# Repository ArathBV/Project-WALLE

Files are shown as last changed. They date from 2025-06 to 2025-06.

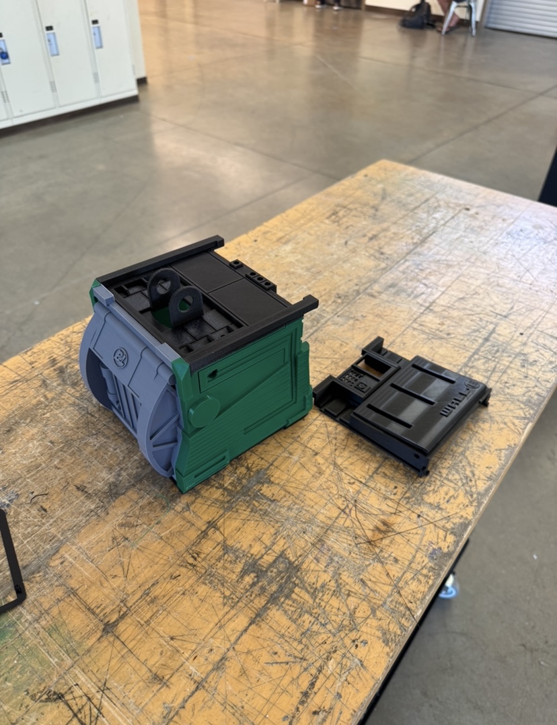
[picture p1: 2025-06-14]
docs/firstPrint.PNG

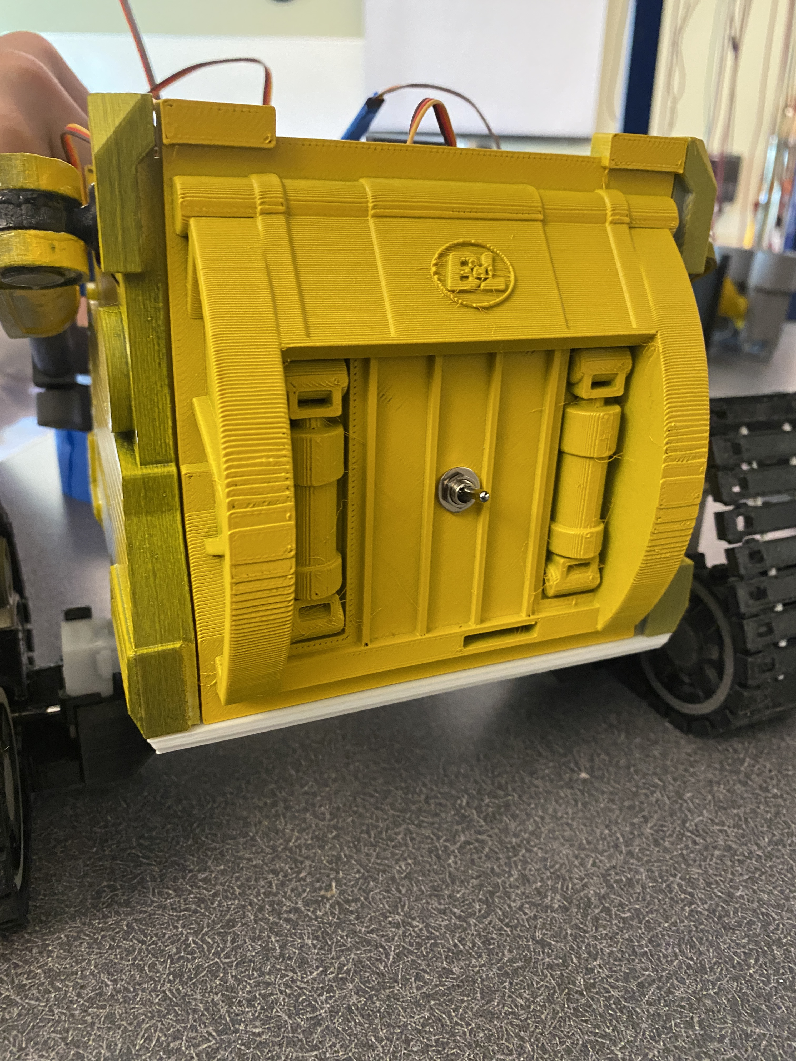
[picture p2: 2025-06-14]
docs/images/WALLE_ESTOP.JPG

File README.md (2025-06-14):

# Project-WALLE
## Authors: Arath Villanueva, Devon Bolt
### Repository Overview
- This repository contains a folder of Doxygen items, WALL-E source code found in Codes, and Hardware Design aspects both mechanical and electrical in the Hardware folder.
### Project Website and Documentation
Project in depth details and website https://arathbv.github.io/Project-WALLE/index.html

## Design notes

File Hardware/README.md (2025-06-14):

# WALL-E Hardware Files
- This folder contains the Mechanical design files and the PCB design files. 
- The Mechanical desing components were changed based on the electronic and peripherals that were used for this WALL-E project.
- The WALL-E PCB Folder contains the WALL-E motheboard that was created for this project
- All original and remaining WALL-E CAD and step files can be found at https://wired.chillibasket.com/3d-printed-wall-e/

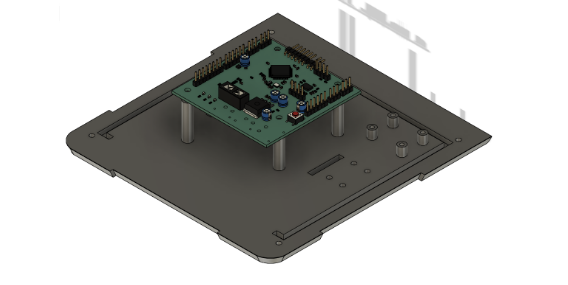
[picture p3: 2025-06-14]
docs/BottomPanelCAD.png

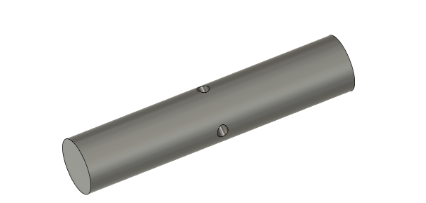
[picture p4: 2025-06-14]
docs/HandAxleCAD.png

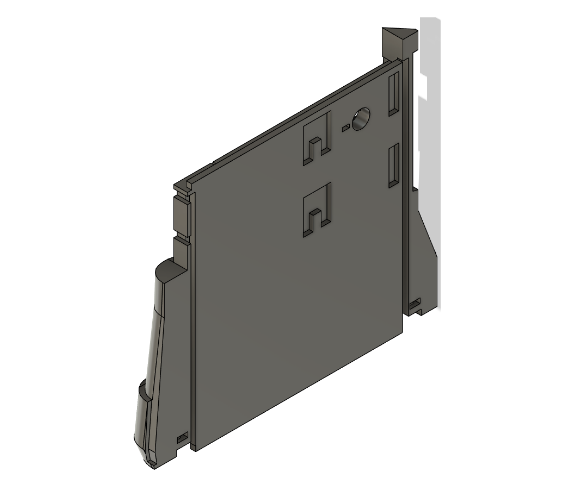
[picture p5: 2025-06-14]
docs/RightBodyPanelCAD.png

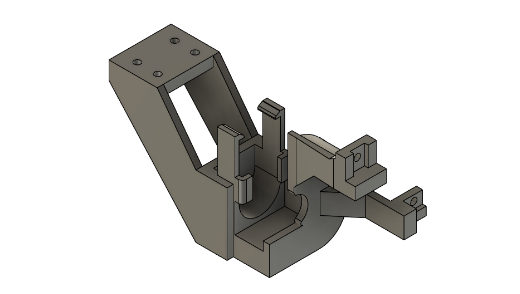
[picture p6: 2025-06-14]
docs/MotorMountCAD.png

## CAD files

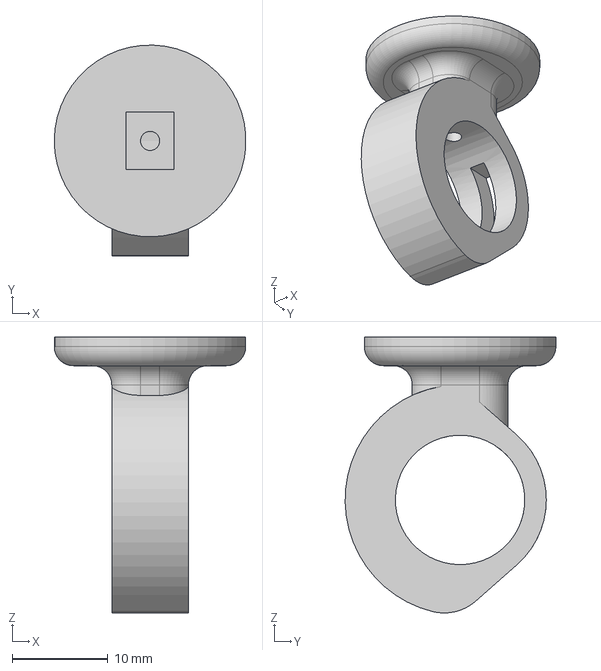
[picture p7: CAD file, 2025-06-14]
Hardware/Mechanical Design Modified Files/Arm Files/arm-hinge-outer-x2 v3.step
20.0 x 22.0 x 28.8 mm

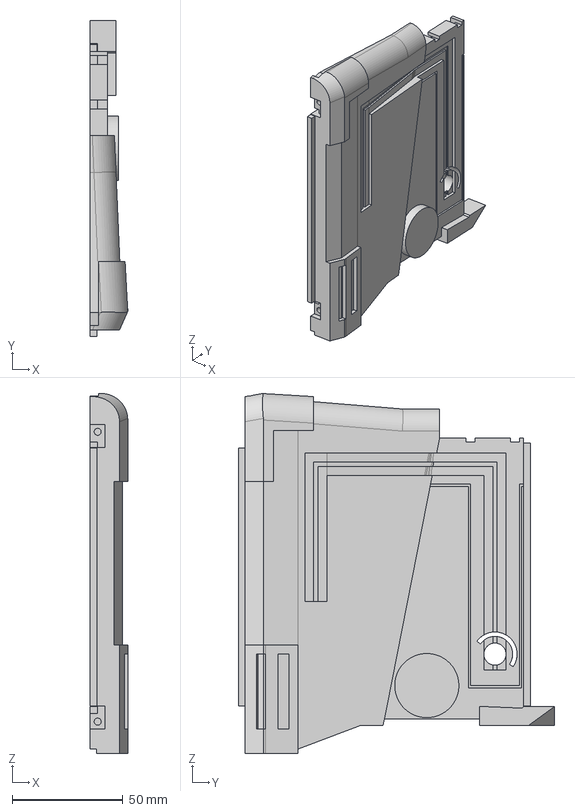
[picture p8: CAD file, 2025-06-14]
Hardware/Mechanical Design Modified Files/Body Files/body-left v4.step
17.0 x 143.0 x 162.7 mm

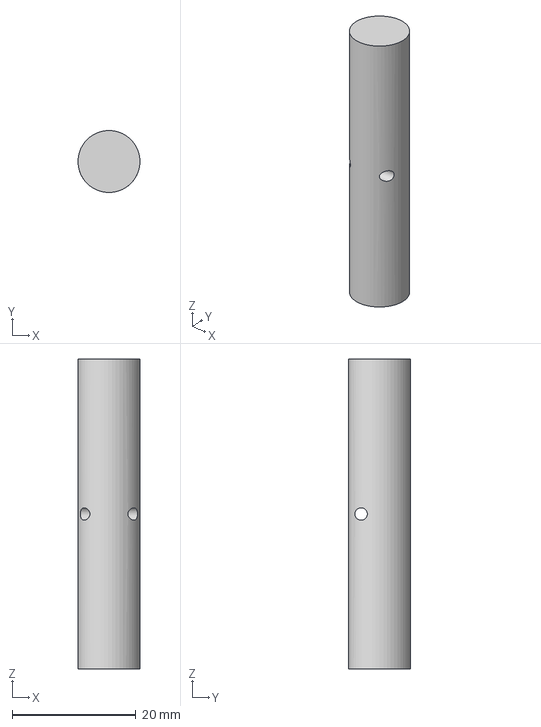
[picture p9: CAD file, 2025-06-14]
Hardware/Mechanical Design Modified Files/Hand Files/hand-axel-x2 v2.step
9.99 x 10.00 x 50.0 mm

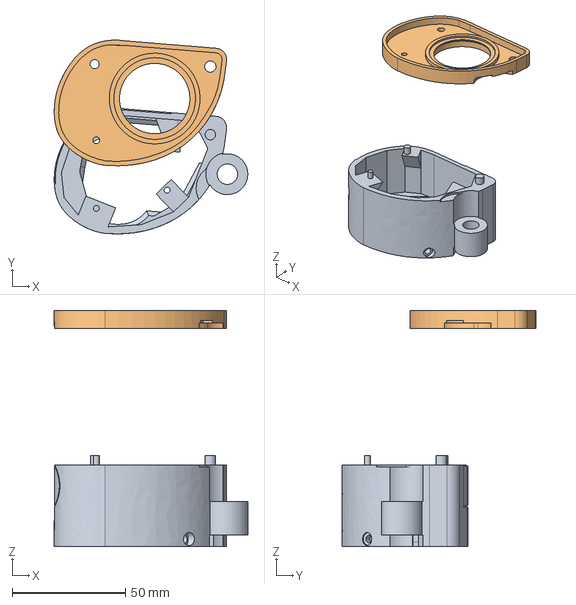
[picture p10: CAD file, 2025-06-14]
Hardware/Mechanical Design Modified Files/Head Files/eye-front-right v11.step
85.3 x 85.4 x 104.0 mm

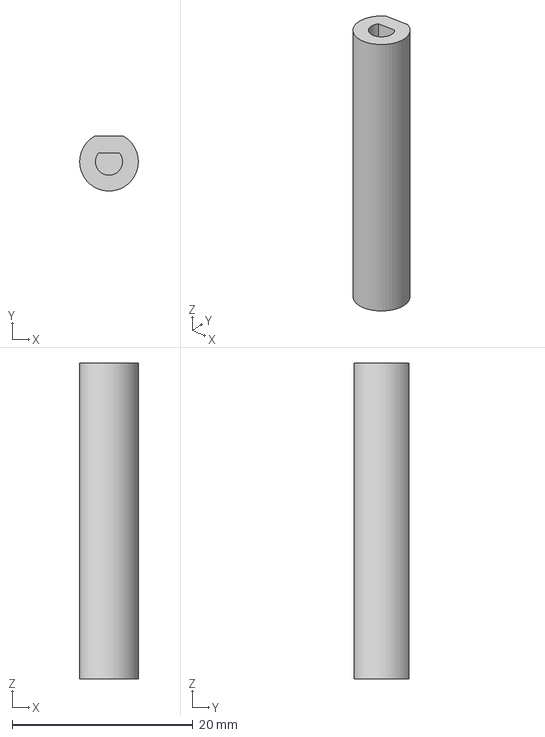
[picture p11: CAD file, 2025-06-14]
Hardware/Mechanical Design Modified Files/Wheel Files/wheel-bracket-outer-left v10.step
6.50 x 6.09 x 35.0 mm

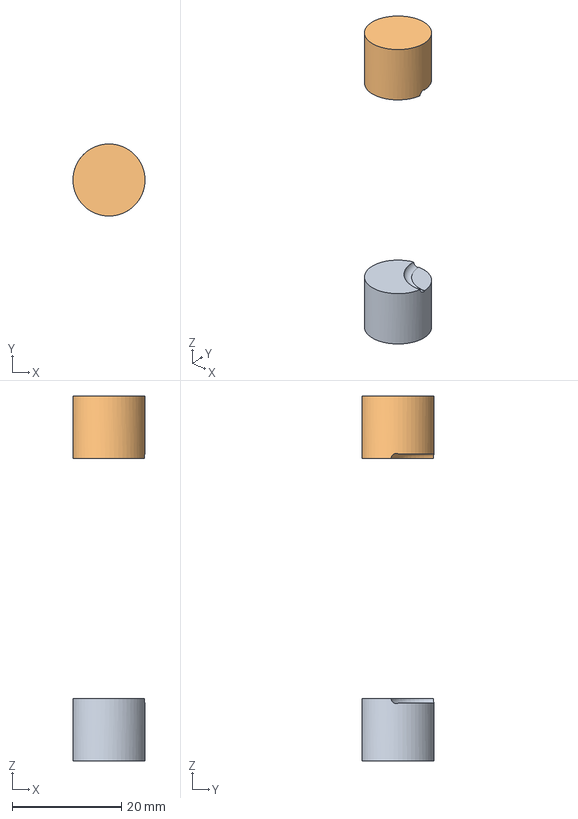
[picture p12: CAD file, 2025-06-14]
Hardware/Mechanical Design Modified Files/Arm Files/arm-hinge-axel-x2 v3.step
13.2 x 13.2 x 66.8 mm

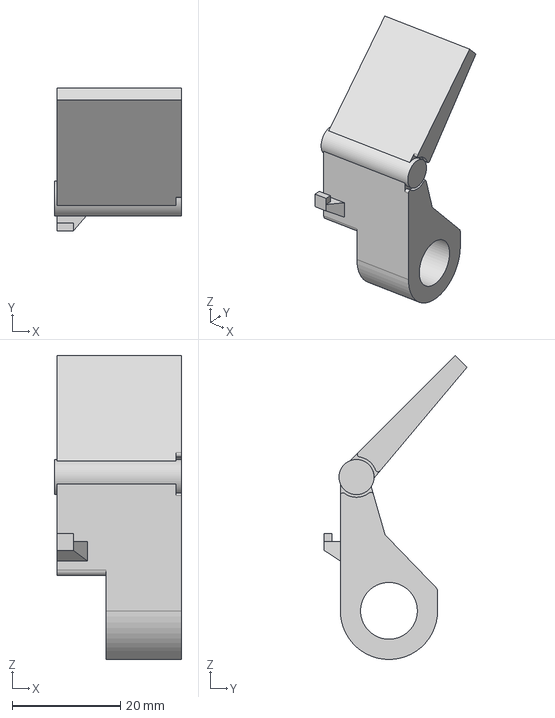
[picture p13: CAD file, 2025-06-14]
Hardware/Mechanical Design Modified Files/Hand Files/hand-finger-left-x2 v2.step
23.5 x 26.4 x 56.2 mm

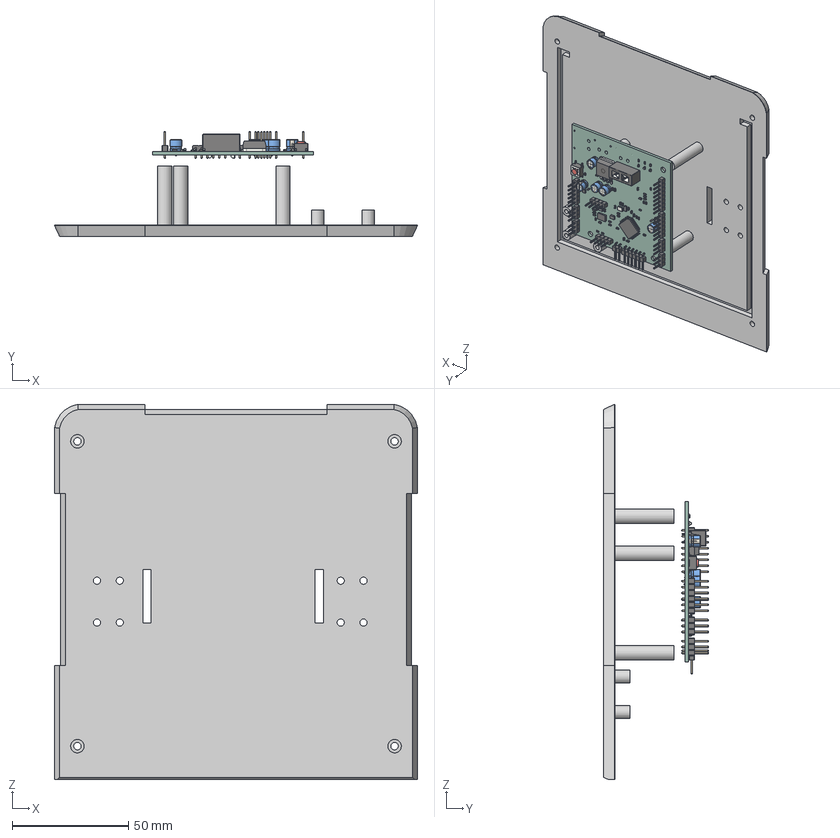
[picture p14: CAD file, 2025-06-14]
Hardware/Mechanical Design Modified Files/Body Files/body-bottom v12.step
156.0 x 45.2 x 161.3 mm
LQFP_64_10x10mm_P05mm
C_0603_1608Metric_23 x 23
R_0603_1608Metric_21 x 21
CP_Radial_D50mm_P200mm x 5
PinHeader_1x06_P254mm_Horizontal
PinHeader_1x02_P254mm_Horizontal
Crystal_SMD_3215-2Pin_3.2x1.5mm_2 x 2
LED_0603_1608Metric_3 x 3
PinHeader_1x04_P254mm_Vertical x 2
PinHeader_1x03_P254mm_Vertical x 4
WSON_8_1EP_2x2mm_P05mm_EP09x16mm x 2
LGA_28_52x38mm_P05mm
A_Keystone_3568
PinHeader_1x06_P254mm_Vertical x 2
PinHeader_1x08_P254mm_Vertical
SW_SPST_PTS645_1
L_1008_2520Metric_1
CQ assembly
Crystal_SMD_3225-4Pin_3.2x2.5mm_1
Wall_E_motherboard_PCB

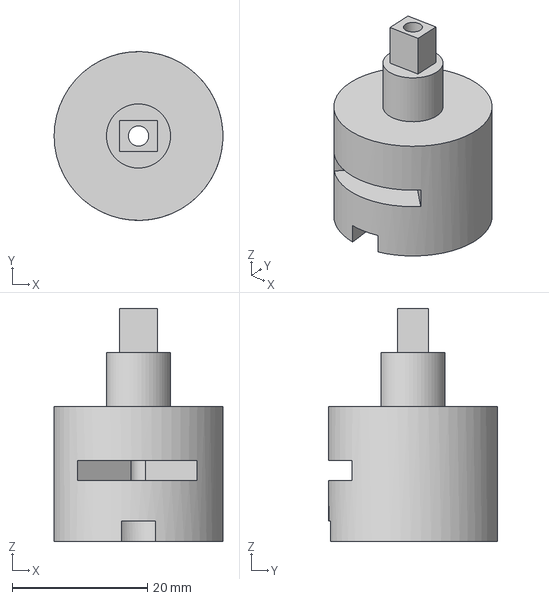
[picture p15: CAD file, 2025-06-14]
Hardware/Mechanical Design Modified Files/Arm Files/arm-hinge-inner-right v4.step
25.0 x 25.0 x 34.5 mm

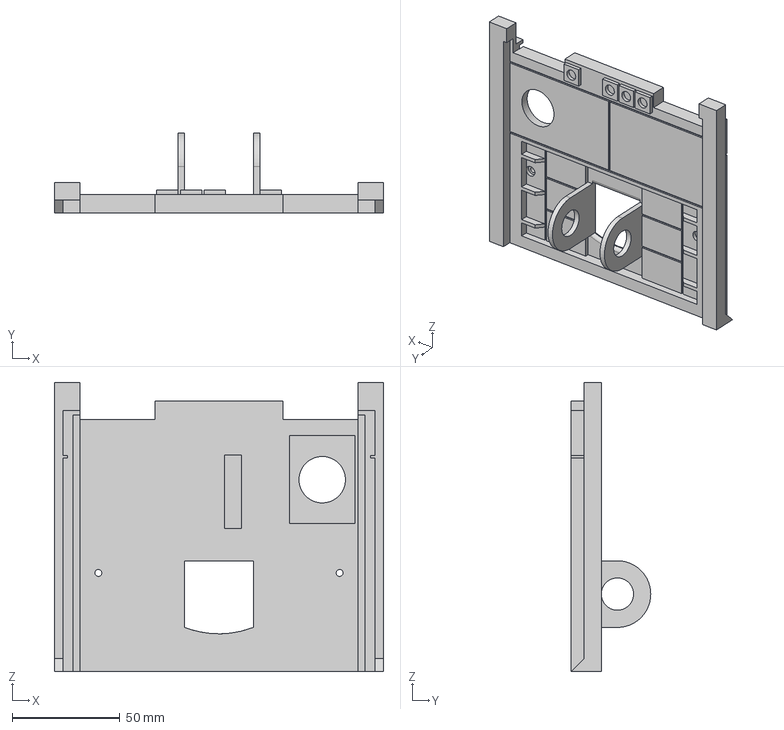
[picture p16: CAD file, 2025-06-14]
Hardware/Mechanical Design Modified Files/Body Files/body-top v2.step
153.0 x 37.0 x 134.4 mm

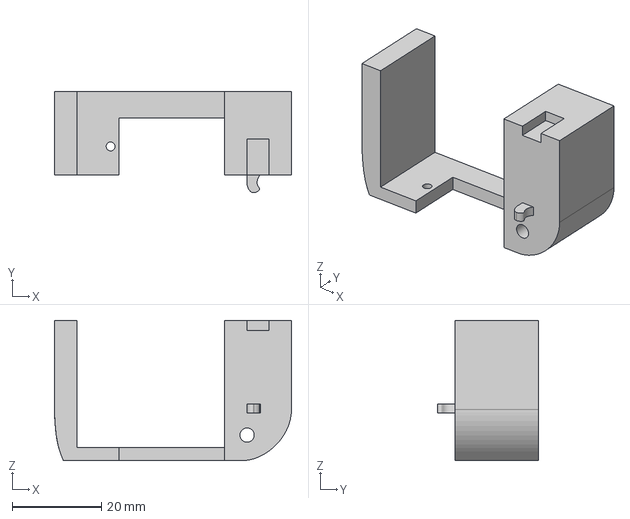
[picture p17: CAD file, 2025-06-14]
Hardware/Mechanical Design Modified Files/Arm Files/arm-servo-bracket-right v2.step
53.2 x 22.8 x 31.5 mm

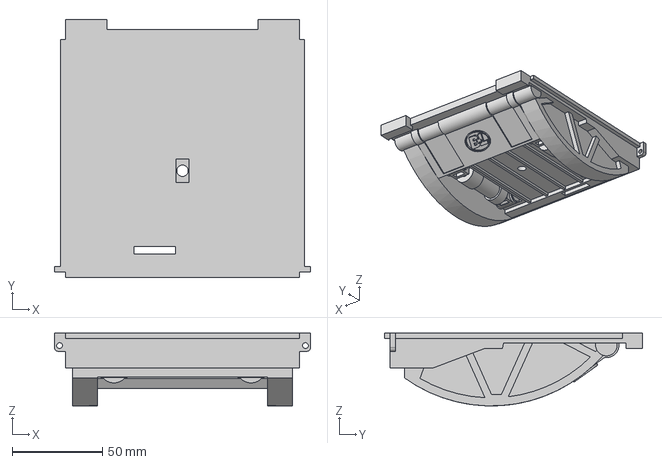
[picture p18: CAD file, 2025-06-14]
Hardware/Mechanical Design Modified Files/Body Files/body-back v3.step
141.9 x 143.0 x 40.3 mm

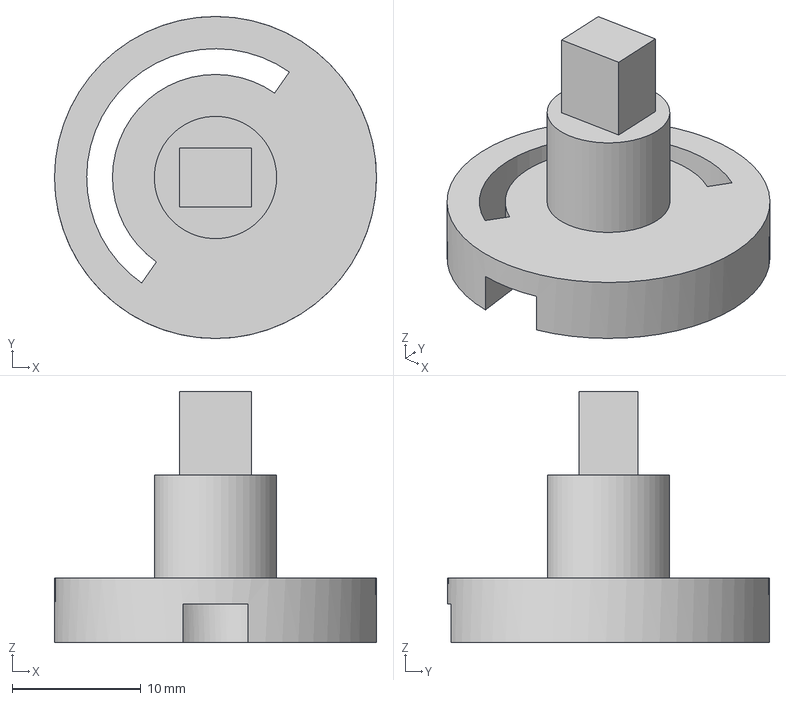
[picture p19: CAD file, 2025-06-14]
Hardware/Mechanical Design Modified Files/Arm Files/arm-hinge-inner-left v2.step
25.0 x 25.0 x 19.5 mm

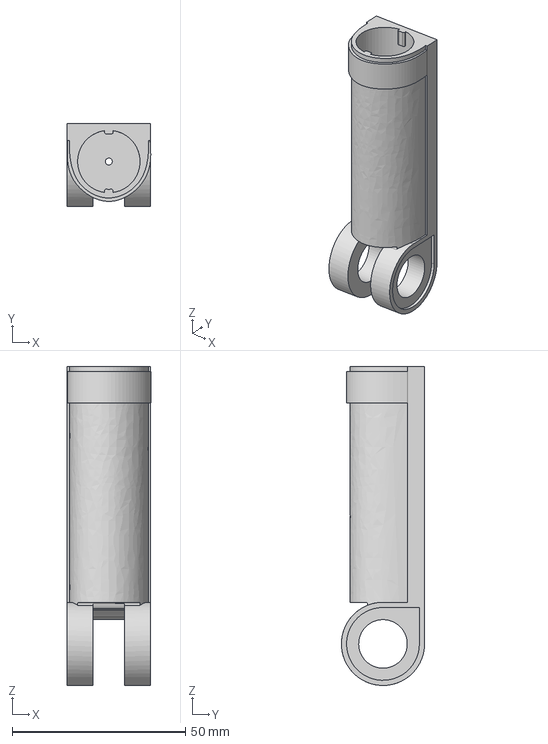
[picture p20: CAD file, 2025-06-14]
Hardware/Mechanical Design Modified Files/Arm Files/arm-barrel-x2 v4.step
24.1 x 24.0 x 92.0 mm

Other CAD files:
Hardware/Mechanical Design Modified Files/Body Files/body-right v3.step
Hardware/Mechanical Design Modified Files/Arm Files/arm-servo-bracket-left v2.step
Hardware/Mechanical Design Modified Files/Arm Files/arm-piston-x2 v5.step
Hardware/Mechanical Design Modified Files/Wheel Files/wheel-bracket-outer-left v2.step
Hardware/Mechanical Design Modified Files/Arm Files/arm-hinge-inner-right v2.step

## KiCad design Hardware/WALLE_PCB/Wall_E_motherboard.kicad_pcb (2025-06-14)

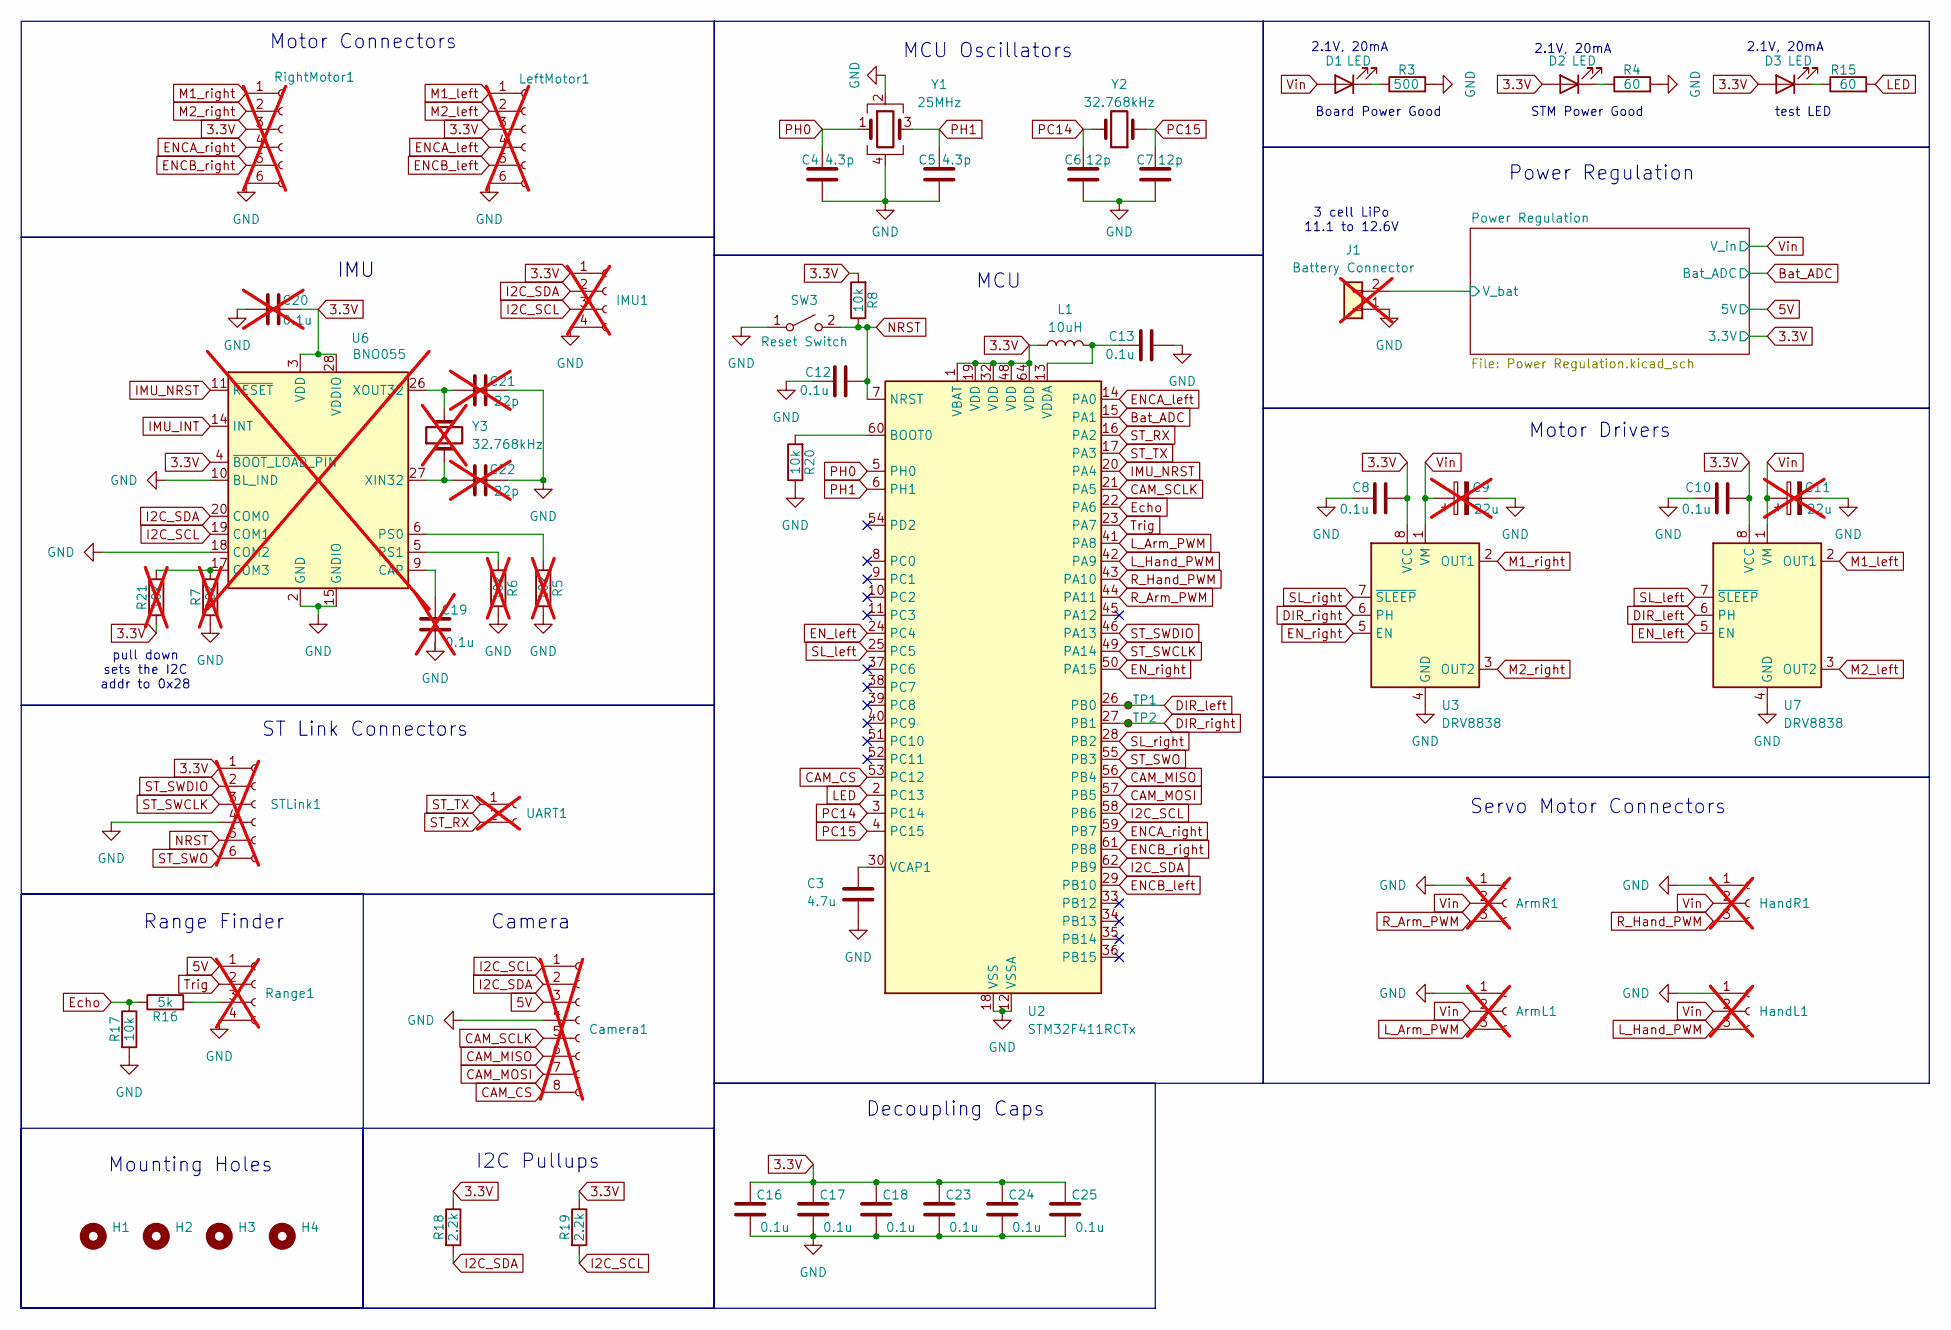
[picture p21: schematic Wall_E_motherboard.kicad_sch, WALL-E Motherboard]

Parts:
ArmL1: Conn_01x03_Socket; PinHeader_1x03_P2.54mm_Vertical; not fitted
ArmR1: Conn_01x03_Socket; PinHeader_1x03_P2.54mm_Vertical; not fitted
C3: 4.7u; C_0603_1608Metric
C4, C5: 4.3p; C_0603_1608Metric
C6, C7: 12p; C_0603_1608Metric
C8, C10, C12, C13, C16, C17, C18, C23, C24, C25: 0.1u; C_0603_1608Metric
C9, C11: 22u; CP_Radial_D5.0mm_P2.00mm; not fitted
C19, C20: 0.1u; C_0603_1608Metric; not fitted
C21, C22: 22p; C_0603_1608Metric; not fitted
Camera1: Conn_01x08_Socket; PinHeader_1x08_P2.54mm_Vertical; not fitted
D1, D2, D3: LED; LED_0603_1608Metric
H1, H2, H3, H4: MountingHole; MountingHole_3.2mm_M3
HandL1: Conn_01x03_Socket; PinHeader_1x03_P2.54mm_Vertical; not fitted
HandR1: Conn_01x03_Socket; PinHeader_1x03_P2.54mm_Vertical; not fitted
IMU1: Conn_01x04_Socket; PinHeader_1x04_P2.54mm_Vertical; not fitted
J1: Conn_01x02; AMASS_XT30PW-M_1x02_P2.50mm_Horizontal; not fitted
L1: 10uH; L_1008_2520Metric
LeftMotor1: Conn_01x06_Socket; PinHeader_1x06_P2.54mm_Vertical; not fitted
R3: 500; R_0603_1608Metric
R4, R15: 60; R_0603_1608Metric
R5, R6, R7, R21: 10k; R_0603_1608Metric; not fitted
R8, R17, R20: 10k; R_0603_1608Metric
R16: 5k; R_0603_1608Metric
R18, R19: 2.2k; R_0603_1608Metric
Range1: Conn_01x04_Socket; PinHeader_1x04_P2.54mm_Vertical; not fitted
RightMotor1: Conn_01x06_Socket; PinHeader_1x06_P2.54mm_Vertical; not fitted
STLink1: Conn_01x06_Socket; PinHeader_1x06_P2.54mm_Horizontal; not fitted
SW3: SW_SPST; SW_SPST_PTS645
TP1, TP2: TestPoint_Small; TestPoint_Pad_D1.0mm
U2: STM32F411RCTx; LQFP-64_10x10mm_P0.5mm
U3, U7: DRV8838; WSON-8-1EP_2x2mm_P0.5mm_EP0.9x1.6mm
U6: BNO055; LGA-28_5.2x3.8mm_P0.5mm; not fitted
UART1: Conn_01x02_Socket; PinHeader_1x02_P2.54mm_Horizontal; not fitted
Y1: 25MHz; Crystal_SMD_3225-4Pin_3.2x2.5mm
Y2: 32.768kHz; Crystal_SMD_3215-2Pin_3.2x1.5mm
Y3: 32.768kHz; Crystal_SMD_3215-2Pin_3.2x1.5mm; not fitted

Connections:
3.3V: C8.1, C10.1, C16.1, C17.1, C18.1, C20.2, C23.1, C24.1, C25.1, D2.2 (A), D3.2 (A), IMU1.1, L1.1, LeftMotor1.3, R8.2, R18.1, R19.1, R21.2, RightMotor1.3, STLink1.1, U2.1 (VBAT), U2.19 (VDD), U2.32 (VDD), U2.48 (VDD), U2.64 (VDD), U3.8 (VCC), U6.3 (VDD), U6.4 (~BOOT_LOAD_PIN), U6.28 (VDDIO), U7.8 (VCC); also elsewhere on the board
5V: Camera1.3, Range1.1; also elsewhere on the board
/Power Regulation/V_bat: J1.2; also elsewhere on the board
Bat_ADC: U2.15 (PA1); also elsewhere on the board
CAM_CS: Camera1.8, U2.53 (PC12)
CAM_MISO: Camera1.6, U2.56 (PB4)
CAM_MOSI: Camera1.7, U2.57 (PB5)
CAM_SCLK: Camera1.5, U2.21 (PA5)
DIR_left: TP1.1, U2.26 (PB0), U7.6 (PH)
DIR_right: TP2.1, U2.27 (PB1), U3.6 (PH)
ENCA_left: LeftMotor1.4, U2.14 (PA0)
ENCA_right: RightMotor1.4, U2.59 (PB7)
ENCB_left: LeftMotor1.5, U2.29 (PB10)
ENCB_right: RightMotor1.5, U2.61 (PB8)
EN_left: U2.24 (PC4), U7.5 (EN)
EN_right: U2.50 (PA15), U3.5 (EN)
Echo: R16.1, R17.1, U2.22 (PA6)
GND: ArmL1.1, ArmR1.1, C3.2, C4.2, C5.2, C6.2, C7.2, C8.2, C9.2, C10.2, C11.2, C12.2, C13.2, C16.2, C17.2, C18.2, C19.2, C20.1, C21.2, C22.2, C23.2, C24.2, C25.2, Camera1.4, HandL1.1, HandR1.1, IMU1.4, J1.1, LeftMotor1.6, R3.2, R4.2, R5.1, R6.1, R7.2, R17.2, R20.1, Range1.4, RightMotor1.6, STLink1.4, SW3.1 (A), U2.12 (VSSA), U2.18 (VSS), U2.31 (VSS), U2.47 (VSS), U2.63 (VSS), U3.4 (GND), U3.9 (GND), U6.2 (GND), U6.10 (BL_IND), U6.15 (GNDIO), U6.16 (GNDIO), U6.18 (COM2), U6.25 (GNDIO), U7.4 (GND), U7.9 (GND), Y1.2, Y1.4; also elsewhere on the board
I2C_SCL: Camera1.1, IMU1.3, R19.2, U2.58 (PB6), U6.19 (COM1)
I2C_SDA: Camera1.2, IMU1.2, R18.2, U2.62 (PB9), U6.20 (COM0)
IMU_INT: U6.14 (INT)
IMU_NRST: U2.20 (PA4), U6.11 (~RESET)
LED: R15.2, U2.2 (PC13)
L_Arm_PWM: ArmL1.3, U2.41 (PA8)
L_Hand_PWM: HandL1.3, U2.42 (PA9)
M1_left: LeftMotor1.1, U7.2 (OUT1)
M1_right: RightMotor1.1, U3.2 (OUT1)
M2_left: LeftMotor1.2, U7.3 (OUT2)
M2_right: RightMotor1.2, U3.3 (OUT2)
NRST: C12.1, R8.1, STLink1.5, SW3.2 (B), U2.7 (NRST)
unnamed: D1.1 (K), R3.1
unnamed: D2.1 (K), R4.1
unnamed: D3.1 (K), R15.1
unnamed: R16.2, Range1.3
unnamed: R20.2, U2.60 (BOOT0)
unnamed: C3.1, U2.30 (VCAP1)
unnamed: C13.1, L1.2, U2.13 (VDDA)
unnamed: C19.1, U6.9 (CAP)
unnamed: R7.1, R21.1, U6.17 (COM3)
unnamed: R5.2, U6.6 (PS0)
unnamed: R6.2, U6.5 (PS1)
unnamed: C22.1, U6.27 (XIN32), Y3.1
unnamed: C21.1, U6.26 (XOUT32), Y3.2
PC14: C6.1, U2.3 (PC14), Y2.2
PC15: C7.1, U2.4 (PC15), Y2.1
PH0: C4.1, U2.5 (PH0), Y1.1
PH1: C5.1, U2.6 (PH1), Y1.3
R_Arm_PWM: ArmR1.3, U2.44 (PA11)
R_Hand_PWM: HandR1.3, U2.43 (PA10)
SL_left: U2.25 (PC5), U7.7 (~SLEEP)
SL_right: U2.28 (PB2), U3.7 (~SLEEP)
ST_RX: U2.16 (PA2), UART1.2
ST_SWCLK: STLink1.3, U2.49 (PA14)
ST_SWDIO: STLink1.2, U2.46 (PA13)
ST_SWO: STLink1.6, U2.55 (PB3)
ST_TX: U2.17 (PA3), UART1.1
Trig: Range1.2, U2.23 (PA7)
Vin: ArmL1.2, ArmR1.2, C9.1, C11.1, D1.2 (A), HandL1.2, HandR1.2, U3.1 (VM), U7.1 (VM); also elsewhere on the board

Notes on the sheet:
Decoupling Caps
STM Power Good
Board Power Good
Range Finder
Power Regulation
Mounting Holes
Camera
MCU Oscillators
Motor Connectors
Servo Motor Connectors
ST Link Connectors
2.1V, 20mA
IMU
Motor Drivers
I2C Pullups
3 cell LiPo 11.1 to 12.6V
test LED
pull down sets the I2C addr to 0x28
MCU

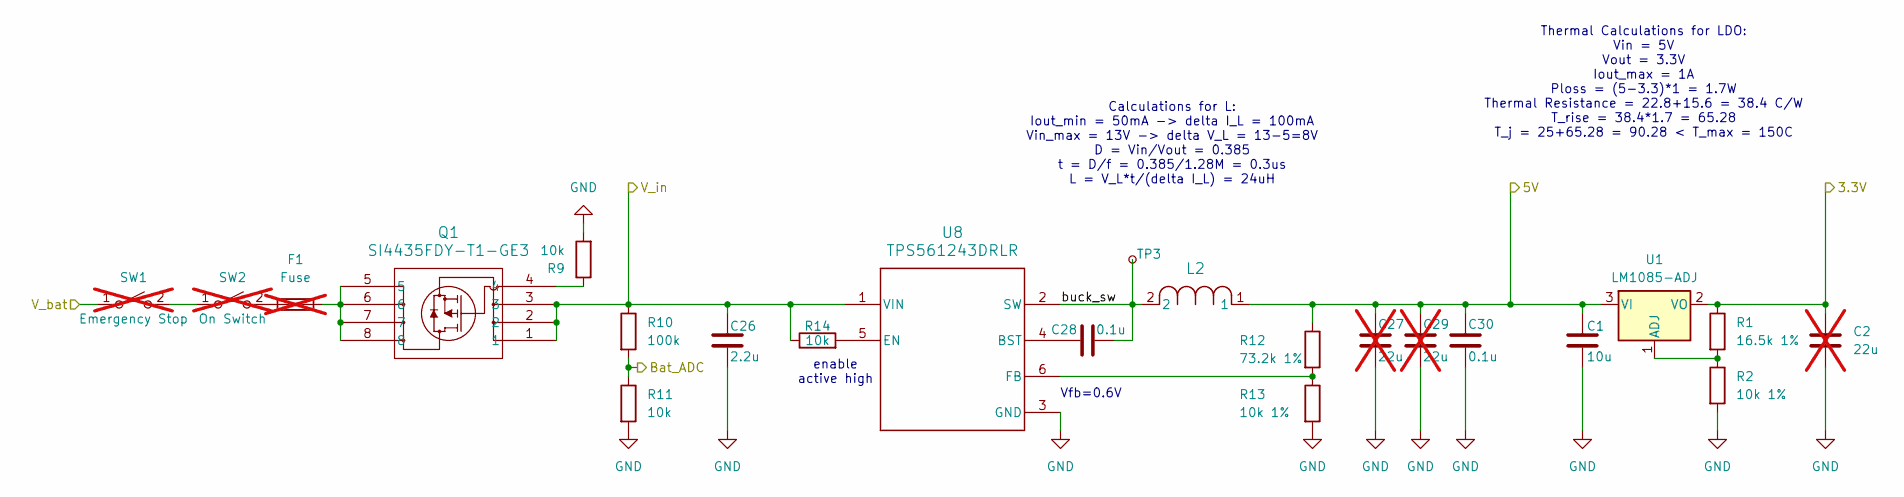
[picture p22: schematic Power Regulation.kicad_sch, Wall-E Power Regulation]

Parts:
C1: 10u; C_0603_1608Metric
C2, C27, C29: 22u; CP_Radial_D5.0mm_P2.00mm; not fitted
C26: 2.2u; C_0603_1608Metric
C28, C30: 0.1u; C_0603_1608Metric
F1: Fuse; Fuseholder_Blade_Mini_Keystone_3568; not fitted
L2: IFDC5050HZER270M; IND_IFDC5050HZER_VIS
Q1: SI4435FDY-T1-GE3; SO-8_VIS
R1: 16.5k 1%; R_0603_1608Metric
R2, R13: 10k 1%; R_0603_1608Metric
R9, R11, R14: 10k; R_0603_1608Metric
R10: 100k; R_0603_1608Metric
R12: 73.2k 1%; R_0603_1608Metric
SW1, SW2: SW_SPST; AMASS_XT30PW-F_1x02_P2.50mm_Horizontal; not fitted
TP3: TestPoint_Small; TestPoint_Pad_D1.0mm
U1: LM1085-ADJ; TO-263-3_TabPin2
U8: TPS561243DRLR; DRL0006A-MFG

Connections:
3.3V: C2.1, R1.1, U1.2 (VO); also elsewhere on the board
5V: C1.1, C27.1, C29.1, C30.1, L2.1, R12.1, U1.3 (VI); also elsewhere on the board
/Power Regulation/V_bat: SW1.1 (A); also elsewhere on the board
/Power Regulation/buck_sw: C28.2, L2.2, TP3.1, U8.2 (SW)
Bat_ADC: R10.2, R11.1; also elsewhere on the board
GND: C1.2, C2.2, C26.2, C27.2, C29.2, C30.2, R2.2, R9.2, R11.2, R13.2, U8.3 (GND); also elsewhere on the board
unnamed: F1.2, Q1.5, Q1.6, Q1.7, Q1.8
unnamed: Q1.4, R9.1
unnamed: SW1.2 (B), SW2.1 (A)
unnamed: F1.1, SW2.2 (B)
unnamed: R1.2, R2.1, U1.1 (ADJ)
unnamed: C28.1, U8.4 (BST)
unnamed: R14.2, U8.5 (EN)
unnamed: R12.2, R13.1, U8.6 (FB)
Vin: C26.1, Q1.1, Q1.2, Q1.3, R10.1, R14.1, U8.1 (VIN); also elsewhere on the board

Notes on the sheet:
Vfb=0.6V
Calculations for L: Iout_min = 50mA -> delta I_L = 100mA Vin_max = 13V -> delta V_L = 13-5=8V D = Vin/Vout = 0.385 t = D/f = 0.385/1.28M = 0.3us L = V_L*t/(delta I_L) = 24uH
enable active high
Thermal Calculations for LDO: Vin = 5V Vout = 3.3V Iout_max = 1A Ploss = (5-3.3)*1 = 1.7W Thermal Resistance = 22.8+15.6 = 38.4 C/W T_rise = 38.4*1.7 = 65.28 T_j = 25+65.28 = 90.28 < T_max = 150C

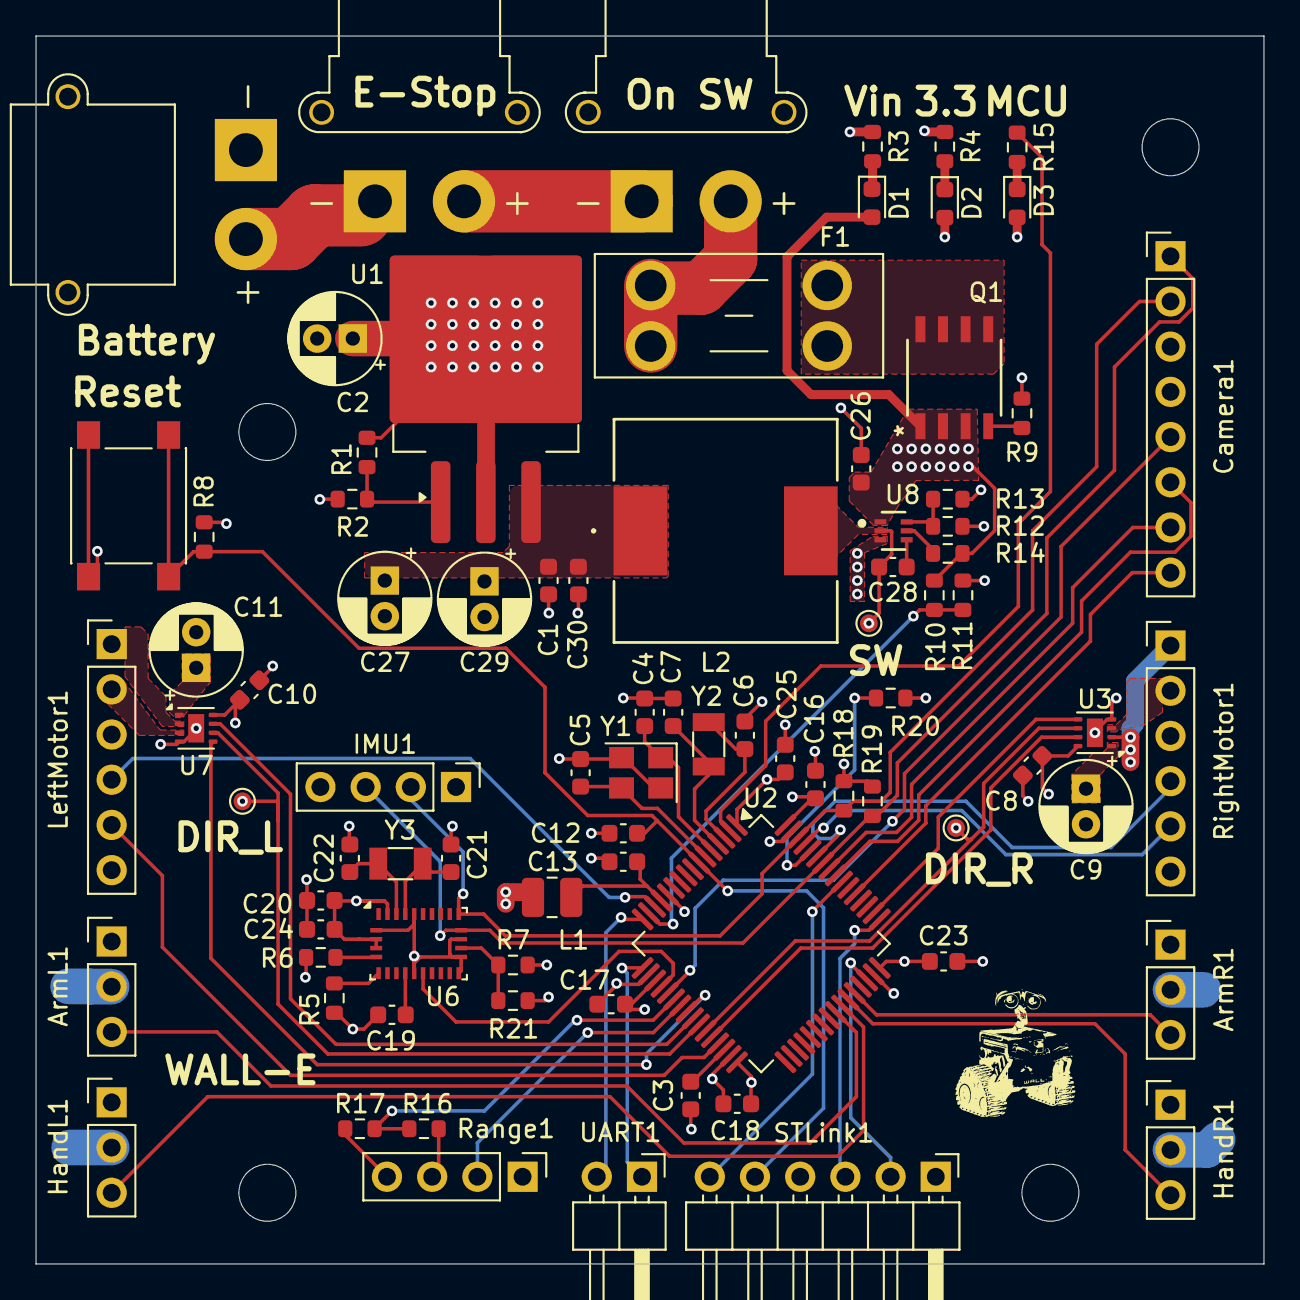
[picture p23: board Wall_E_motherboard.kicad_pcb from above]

Board: 4 copper layers, 69.0 x 69.0 mm, 87 parts (0 on the bottom side), 66 nets.

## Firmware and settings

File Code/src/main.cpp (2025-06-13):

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
/* Includes ------------------------------------------------------------------*/
#include "main.h"
#include "main.h"
#include "batteryMonitor.h"
#include "WALLE_FSM.h"
#include <string.h>
#include <unistd.h>
#include <stdio.h>

ADC_HandleTypeDef hadc1;

I2C_HandleTypeDef hi2c1;

SPI_HandleTypeDef hspi1;

TIM_HandleTypeDef htim1;
TIM_HandleTypeDef htim2;
TIM_HandleTypeDef htim3;
TIM_HandleTypeDef htim4;
TIM_HandleTypeDef htim5;

UART_HandleTypeDef huart2;

/*Global Motors for interrupt updates*/
RomiMotor rightMotor(GPIOA, EN_Right_Pin, GPIOB, DIR_Right_Pin, GPIOB, SL_Right_Pin);
RomiMotor leftMotor(GPIOC, EN_Left_Pin, GPIOB, DIR_Left_Pin, GPIOC, SL_Left_Pin);
void SystemClock_Config(void);
static void MX_GPIO_Init(void);
static void MX_ADC1_Init(void);
static void MX_I2C1_Init(void);
static void MX_TIM1_Init(void);
static void MX_TIM2_Init(void);
static void MX_TIM4_Init(void);
static void MX_USART2_UART_Init(void);
static void MX_TIM3_Init(void);
static void MX_SPI1_Init(void);
static void MX_TIM5_Init(void);

#ifndef WALL_E_FUNC
#define WALL_E_FUNC
void WALL_E_systemCheck(BatteryMonitor&, HCSR04&, RomiMotor&, RomiMotor&, BNO055&, OV2640Camera&);
#endif
/* USER CODE BEGIN PFP */
#define OV2640_I2C_ADDR 0x60  // 0x30 << 1

/* USER CODE END PFP */

/* USER CODE BEGIN 0 */
void printToUART(const char* msg) {
    HAL_UART_Transmit(&huart2, (uint8_t*)msg, strlen(msg), HAL_MAX_DELAY);
}

void simpleMovements(){
	rightMotor.setSpeed(10);
	leftMotor.setSpeed(-10);
	HAL_Delay(1000);
	rightMotor.setSpeed(-5);
	HAL_Delay(500);
	rightMotor.setSpeed(10);
	HAL_Delay(700);
	leftMotor.setSpeed(0);
	rightMotor.setSpeed(0);
}
/* USER CODE END 0 */

/**
  * @brief  The application entry point.
  * @retval int
  */
int main(void)
{

  /* MCU Configuration--------------------------------------------------------*/

  /* Reset of all peripherals, Initializes the Flash interface and the Systick. */
  HAL_Init();

  /* Configure the system clock */
  SystemClock_Config();

  /* Initialize all configured peripherals */
  MX_GPIO_Init();
  MX_ADC1_Init();
  MX_I2C1_Init();
  MX_TIM1_Init();
  MX_TIM2_Init();
  MX_TIM4_Init();
  MX_USART2_UART_Init();
  MX_TIM3_Init();
  MX_SPI1_Init();
  MX_TIM5_Init();

  HAL_NVIC_SetPriority(TIM5_IRQn, 0, 0);
  HAL_NVIC_EnableIRQ(TIM5_IRQn);

  /*Peripherals Instantiation*/
  BatteryMonitor batteryMonitor(&hadc1, 7000);
  HCSR04 rangeFinder(GPIOA, Trig_Pin, Echo_GPIO_Port, Echo_Pin, &htim3);
  BNO055 imu(&hi2c1, (uint8_t) 0x28);
  OV2640Camera camera(&hi2c1, &hspi1, GPIOC, CAM_CS_Pin);
  Servo rightArm(&htim1, TIM_CHANNEL_4);
  Servo rightHand(&htim1, TIM_CHANNEL_3);
  Servo leftArm(&htim1, TIM_CHANNEL_1);
  Servo leftHand(&htim1, TIM_CHANNEL_2);
  rightArm.attach();
  rightHand.attach();
  leftArm.attach();
  leftHand.attach();

  WALL_E_systemCheck(batteryMonitor, rangeFinder, rightMotor, leftMotor, imu, camera);
  printToUART("Entering WALL-E FSM\r\n");

  WALLE walleFSM(imu, rangeFinder, leftMotor, rightMotor, camera, leftArm, leftHand,
		  rightArm, rightHand);

  walleFSM.init();
  uint32_t lastTick = HAL_GetTick();

  while(1){
	  uint32_t currentTick = HAL_GetTick();
	  float dt = (currentTick - lastTick);
	  lastTick = currentTick;

	  walleFSM.update(dt);

	  HAL_Delay(5);

  }

}

/*
 * @brief Function Performs System Peipherals Check
 * @return None
 */
void WALL_E_systemCheck(BatteryMonitor& bat, HCSR04& range, RomiMotor& rMotor, RomiMotor& lMotor, BNO055& imu, OV2640Camera& camera){
	  imu.init_imu();
	  char buffer[1024];
	  uint8_t sys, gyro, accel, mag;
	  while (true) {
		  imu.readCalibStatus(sys, gyro, accel, mag);
		  if (sys == 3 && gyro == 3){
			  int len = sprintf(buffer, "IMU Calibrated Sys: %d Gyro: %d\r\n", sys, gyro);
			  HAL_UART_Transmit(&huart2, (uint8_t *)buffer, len, 10);
			  memset(buffer, 0, sizeof(buffer));
			  break;
		  }
		  int len = sprintf(buffer, "Sys %d, Gyro %d, Accel %d, Mag %d\r\n", sys, gyro, accel, mag);
		  HAL_UART_Transmit(&huart2, (uint8_t *)buffer, len, 10);
		  memset(buffer, 0, sizeof(buffer));
		  HAL_Delay(500);
	  }

	  /*UltraSonic Sensor Timer*/
	  HAL_TIM_Base_Start(&htim3);

	  /*Interrupt Timer for PWM Signal for Motors*/
	  rMotor.enable();
	  rMotor.setSpeed(0);
	  lMotor.enable();
	  lMotor.setSpeed(0);
	  HAL_TIM_Base_Start_IT(&htim5);
	  int len = sprintf(buffer, "Motors Enabled, Speed Set to 0.\r\n");
	  HAL_UART_Transmit(&huart2, (uint8_t *)buffer, len, 10);
	  memset(buffer, 0, sizeof(buffer));

	  /*Battery Check*/
	  len = sprintf(buffer, "Battery Voltage is at %u mV\r\nChecking RangeSensor\r\n", bat.getVoltage_mV());
	  HAL_UART_Transmit(&huart2, (uint8_t *)buffer, len, 10);
	  memset(buffer, 0, sizeof(buffer));

	  /*Range Sensor Check*/
	  while(true){
		  bool success = range.measure();
		  if (success){
				  uint32_t d = range.getDistanceCm();
				  len = sprintf(buffer, "\tDistance is %lu cm\r\n", d);
				  HAL_UART_Transmit(&huart2, (uint8_t *)buffer, len, 10);
				  memset(buffer, 0, sizeof(buffer));
				  break;
		  HAL_Delay(500);
		  }
	  }

	  /*Camera Check*/
	  printToUART("Camera I2C Check and initialization\r\n");
	  uint8_t pid = 0, ver = 0;
	  HAL_I2C_Mem_Read(&hi2c1, OV2640_I2C_ADDR, 0x0A, I2C_MEMADD_SIZE_8BIT, &pid, 1, HAL_MAX_DELAY);
	  HAL_I2C_Mem_Read(&hi2c1, OV2640_I2C_ADDR, 0x0B, I2C_MEMADD_SIZE_8BIT, &ver, 1, HAL_MAX_DELAY);

	  char buf[64];
	  snprintf(buf, sizeof(buf), "\tOV2640 PID: 0x%02X, VER: 0x%02X\r\n", pid, ver);
	  HAL_UART_Transmit(&huart2, (uint8_t*)buf, strlen(buf), HAL_MAX_DELAY);
	  while(true){
		  bool success = camera.initialize();
		  if (success){
			  printToUART("\tCamera Initialized. Ready to Detect\r\n");
			  break;
		  }
	  }

}

/*
 * @brief Function is the interrupt Callback for the Updates on the Motor PWM signals
 * @return None
 */
void HAL_TIM_PeriodElapsedCallback(TIM_HandleTypeDef *htim) {
    if (htim->Instance == TIM5) {
        // Your motor PWM logic here
    	rightMotor.updatePWM();
        leftMotor.updatePWM();
    }
}
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


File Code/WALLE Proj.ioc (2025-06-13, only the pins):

Mcu.UserName=STM32F411RCTx
PA0-WKUP.GPIO_Label=ENCA_Left
PA0-WKUP.Signal=S_TIM2_CH1_ETR
PA1.GPIO_Label=Bat_ADC
PA1.Signal=ADCx_IN1
PA10.GPIO_Label=R_HandPWM
PA10.Signal=S_TIM1_CH3
PA11.GPIO_Label=R_ArmPWM
PA11.Signal=S_TIM1_CH4
PA13.Signal=SYS_JTMS-SWDIO
PA14.Signal=SYS_JTCK-SWCLK
PA15.GPIO_Label=EN_Right
PA15.Signal=GPIO_Output
PA2.Signal=USART2_TX
PA3.Signal=USART2_RX
PA4.GPIO_Label=IMU_NRST
PA4.Signal=GPIO_Output
PA5.GPIO_Label=CAM_SCLK
PA5.Signal=SPI1_SCK
PA6.GPIO_Label=Echo
PA6.Signal=GPIO_Input
PA7.GPIO_Label=Trig
PA7.Signal=GPIO_Output
PA8.GPIO_Label=L_ArmPWM
PA8.Signal=S_TIM1_CH1
PA9.GPIO_Label=L_HandPWM
PA9.Signal=S_TIM1_CH2
PB0.GPIO_Label=DIR_Left
PB0.Signal=GPIO_Output
PB1.GPIO_Label=DIR_Right
PB1.Signal=GPIO_Output
PB10.GPIO_Label=ENCB_Left
PB10.Signal=S_TIM2_CH3
PB2.GPIO_Label=SL_Right
PB2.Signal=GPIO_Output
PB3.Signal=SYS_JTDO-SWO
PB4.GPIO_Label=CAM_MISO
PB4.Signal=SPI1_MISO
PB5.GPIO_Label=CAM_MOSI
PB5.Signal=SPI1_MOSI
PB6.Signal=I2C1_SCL
PB7.GPIO_Label=ENCA_Right
PB7.Signal=S_TIM4_CH2
PB8.GPIO_Label=ENCB_Right
PB8.Signal=S_TIM4_CH3
PB9.Signal=I2C1_SDA
PC12.GPIO_Label=CAM_CS
PC12.Signal=GPIO_Output
PC13-ANTI_TAMP.GPIO_Label=LED_PIN
PC13-ANTI_TAMP.Signal=GPIO_Output
PC4.GPIO_Label=EN_Left
PC4.Signal=GPIO_Output
PC5.GPIO_Label=SL_Left
PC5.Signal=GPIO_Output

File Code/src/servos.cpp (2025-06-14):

/* USER CODE BEGIN Header */
/**
  ******************************************************************************
  * @file           : servos.cpp
  * @brief          : File containing the functions to the servo
  * @author			: Arath Villanueva (abvillan@calpoly.edu) Devon Bolt (dwbolt@calpoly.edu)
  ******************************************************************************
  * @attention
  *
  * Copyright (c) 2025 STMicroelectronics.
  * All rights reserved.
  *
  * This software is licensed under terms that can be found in the LICENSE file
  * in the root directory of this software component.
  * If no LICENSE file comes with this software, it is provided AS-IS.
  *
  ******************************************************************************
  */
#include "servos.h"


/**
 * @brief Constructor Function for Servo Motor Class
 */
Servo::Servo(TIM_HandleTypeDef* htim, uint32_t channel)
    : htim(htim), channel(channel) {}

/**
 * @brief Function starts the PWM Channel for the Servo Movement
 * @return None
 */
void Servo::attach() {
    HAL_TIM_PWM_Start(htim, channel);
}

/**
 * @brief Function stops the PWM Signal received from the PWM
 * @return None
 */
void Servo::detach() {
    HAL_TIM_PWM_Stop(htim, channel);
}

/**
 * @brief Function sets the Servo's motor pulse width to determin the angle at which
 * the servo moves to or holds
 * @param pulse_us Parameter that determines what pulse to send to set the Servo to a specified angle
 * @return None
 */
void Servo::setPulseWidth(uint16_t pulse_us) {
    if (pulse_us < 1000) pulse_us = 1000;
    //if (pulse_us > 2500) pulse_us = 2500;

    __HAL_TIM_SET_COMPARE(htim, channel, pulse_us);  // Each tick = 1 µs
}

/**
 * @brief Function set's the Servo motor's pulse width based on the desired angle from the servo.
 * @param angleDeg Parameter that sets the servo to a position based on the actual angle rather than pulse
 * @return None
 */
void Servo::setAngle(uint8_t angleDeg) {
	// Clamp angle to [0,180]
	if (angleDeg > 200) angleDeg = 200;

	// Map angle to pulse width in microseconds
	uint16_t pulse = 500 + ((uint16_t)angleDeg * 2000) / 180;  // 500–2500 µs

    setPulseWidth(pulse);
}

/**
 * @brief Function calculates the angle requested to the PWM pulse that is needed to create the angle.
 * @param angleDeg Parameter that takes in the desired angle and translate to the pulse necessary to set the servo
 * @return uint16_t
 */
uint16_t Servo::angleToPulse(uint8_t angleDeg) {
    // Linear map: 0° → 1000 µs, 180° → 2000 µs
    return 1000 + ((angleDeg * 1000) / 180);  // No floats used
}

/**
 * @brief Function sets Servo to start to stop angle incrementing till requested angle
 * @param angle1 Parameter sets the starting angle to move the servo in a sequence
 * @param angle2 Parameter sets the ending angle to move the servo in a sequence
 * @return None
 */
void Servo::startStopAngle(uint8_t angle1, uint8_t angle2){
	uint8_t start = angle1;
	if (start < angle2){
		while(start != angle2){
			setAngle(start);
			start += 10;
			if (start > angle2)
				start = angle2;
			HAL_Delay(50);
		}
		while(start != angle1){
			setAngle(start);
			start -= 10;
			if (start < angle1)
				start = angle2;
			HAL_Delay(50);
		}
	}else{
		while(start != angle2){
			setAngle(start);
			start -= 10;
			if (start < angle2)
				start = angle2;
			HAL_Delay(50);
		}
		while(start != angle1){
			setAngle(start);
			start += 10;
			if (start > angle1)
				start = angle2;
			HAL_Delay(50);
		}

	}
}

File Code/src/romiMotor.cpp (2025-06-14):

/* USER CODE BEGIN Header */
/**
  ******************************************************************************
  * @file           : romiMotor.cpp
  * @brief          : File containing the functions to the ROMI Motors class
  * @author Arath Villanueva (abvillan@calpoly.edu) Devon Bolt (dwbolt@calpoly.edu)
  ******************************************************************************
  * @attention
  *
  * Copyright (c) 2025 STMicroelectronics.
  * All rights reserved.
  *
  * This software is licensed under terms that can be found in the LICENSE file
  * in the root directory of this software component.
  * If no LICENSE file comes with this software, it is provided AS-IS.
  *
  ******************************************************************************
  */

#include "romiMotor.h"
#include "main.h"
#include <cmath>
//
//#define OV2640_I2C_ADDR 0x60  // 0x30 << 1


/**
 * @brief Construction for the ROMI Motor Class
 */
RomiMotor::RomiMotor(GPIO_TypeDef* enPort, uint16_t enPin,
		GPIO_TypeDef* phPort, uint16_t phPin,
		GPIO_TypeDef* slPort, uint16_t slPin): en_Port(enPort), en_Pin(enPin),
		ph_Port(phPort), ph_Pin(phPin), sl_Port(slPort), sl_Pin(slPin), duty_Cycle(0),
		pwm_Counter(0){}

/**
 * @brief Function Enables the motor to operate based on the PWM
 * @return None
 */
void RomiMotor::enable(){
	HAL_GPIO_WritePin(sl_Port, sl_Pin, GPIO_PIN_SET);
	//HAL_GPIO_WritePin(en_Port, en_Pin, GPIO_PIN_SET);
}

/**
 * @brief Function disables the motor to no longer respond to pwm signals
 * @return None
 */
void RomiMotor::disable(){
	HAL_GPIO_WritePin(sl_Port, sl_Pin, GPIO_PIN_RESET);

}

/**
 * @brief Function Sets the Direction of the PWM Signal and changes direction based
 * on the duty value
 * @param speed Parameter that sets the Romi Motor speed ranging from -100 to 100
 * @return None
 */
void RomiMotor::setSpeed(int8_t speed){
	if (speed > 100) speed = 100;
	if (speed < -100) speed = -100;

	duty_Cycle = abs(speed);
    HAL_GPIO_WritePin(ph_Port, ph_Pin, (speed <= 0) ? GPIO_PIN_SET : GPIO_PIN_RESET);
}

/**
 * @brief Function uses and internal timer to trigger PWM signals via this function through the use
 * of the PWM/Duty Cycle Given
 * @return None
 */
void RomiMotor::updatePWM(){
	pwm_Counter = (pwm_Counter + 1) % 100;
	if (duty_Cycle == 0){
		HAL_GPIO_WritePin(en_Port, en_Pin, GPIO_PIN_RESET);
	}

	else if (pwm_Counter < duty_Cycle){
		HAL_GPIO_WritePin(en_Port, en_Pin, GPIO_PIN_SET);
	}
	else{
		HAL_GPIO_WritePin(en_Port, en_Pin, GPIO_PIN_RESET);
	}
}

/**
 * @brief Function allows the user to get the current duty
 * @return int8_t
 */
int8_t RomiMotor::getDuty(){
	return duty_Cycle;
}

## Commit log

2025-06-13 Commented Camera Files
2025-06-14 WALLE PCB Folder
    [Power Regulation.kicad_sch, Wall_E_motherboard.kicad_pcb, Wall_E_motherboard.kicad_sch]
2025-06-14 WALL-E Modified Step Files
    [arm-barrel-x2 v4.step, arm-hinge-axel-x2 v3.step, arm-hinge-inner-left v2.step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]
2025-06-14 Sensor Page Complete
